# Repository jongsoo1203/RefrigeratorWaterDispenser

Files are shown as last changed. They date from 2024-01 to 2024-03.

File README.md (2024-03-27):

# 🛜 Smart Refrigerator Water Dispenser

Schematics, code, [Web-app](https://github.com/loty2019/water-dispenser-web) and [3D files](https://github.com/loty2019/RefrigeratorWaterDispenser/tree/RelayWaterDispenser/STL%20files) all available.

## ℹ️ Overview
This project aims to automate the refrigerator water dispenser. Originally located inside the fridge, it has been moved outside using a custom 3D-designed fountain. We first prototyped it on Arduino and then transitioned to the ESP32 platform with internet capabilities. The entire system now operates on a real-time database hosted on Firebase.

### Purpose (Why should this exist?)

The fridge has an internal water dispensing system that is manual. You have to hold the water bottle up, then at the same time press a hard button. In this process, the refrigerator loses coldness, and you get cold. Our system, however, utilizes an external custom-designed fountain that provides cold water after just 2 seconds of water flowing with no need to hold or press anything.

## 🗂️ Features

### 1. Remote Control

Our system reads signals from a remote controller, a simple numeric keypad used to navigate menus, set parameters, and choose which water bottle to fill and how.

### 2. Display

The 1602 display with I2C protocol provides real-time information.

### 3. Motion Activation

We've integrated a motion sensor that wakes the device from deep sleep only when someone approaches for water, enhancing energy efficiency.

### 4. Web App

We chose to use Next.js, React and Tailwind CSS to develop a simple yet useful UI to keep track of the water consumption of each user.

### 5. Custom Feature

Hosting guests or following a recipe that demands an exact amount of water? Input the desired ounces, enable unlimited fill, and so on... a handy extra feature for any occasion.

### 6. Relay

To communicate with the fridge on when to open the flow, we decided to use a relay since it allows handling 120V currents with just a 3.3V board.

### 7. Internet

Everything from water consumption to settings will be stored on a Firebase real-time database.

## Settings, Error Handling, and Details

We calculated the dispenser's flow rate and programmed the ESP to adjust the dispensing time accordingly. The user can also adjust it, and everything will be stored on the Flash memory and the database.

### Error Documentation:
Error #01 = Failed to record individual water consumption.

Error #02 = Failed to push consumption to the database.

Error #03 = Failed to generate date or hour due to connection issues.

Others coming soon...

### How to Build (soldering might be required)

- Follow the schematics and picture attached below (these are for the prototype) if you are not using the I2C protocol to cominicate with the display then use a NPN transistor to turn off the screen.
  I actually used a 3 pin relay so the image below is not accurate

[Water Dispenser.pdf](https://github.com/loty2019/RefrigeratorWaterDispenser/files/13521786/Water.Dispenser.pdf)

- 3D printable files are in STL_files folder
3D design
fusion fauntain v2

- Set up a database and a web app

Screenshot 2024-03-16 at 11 35 05 AM

- Final Product


https://github.com/loty2019/RefrigeratorWaterDispenser/assets/125715080/05de6919-4a6a-43a9-aefa-cd7f2b6fba2c

Collaboration: Lorenzo, Jongsoo, Minh

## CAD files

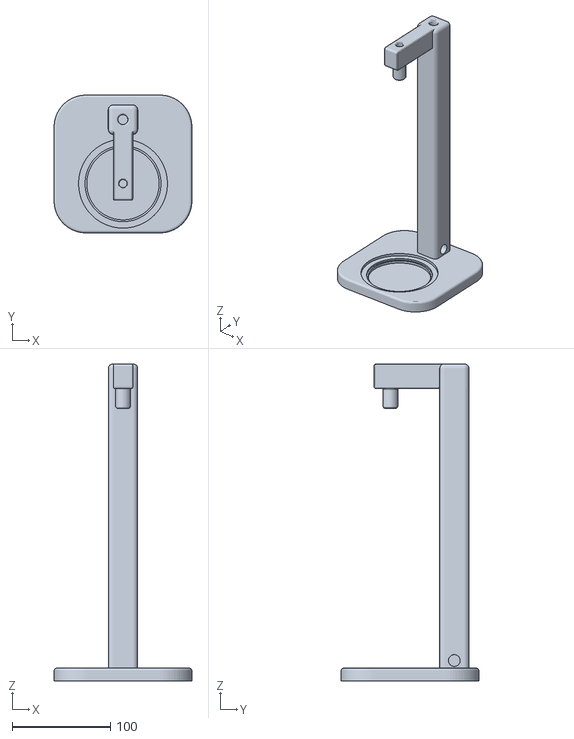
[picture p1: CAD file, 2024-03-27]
STL files/fauntain v2.stl
140.0 x 140.0 x 321.9

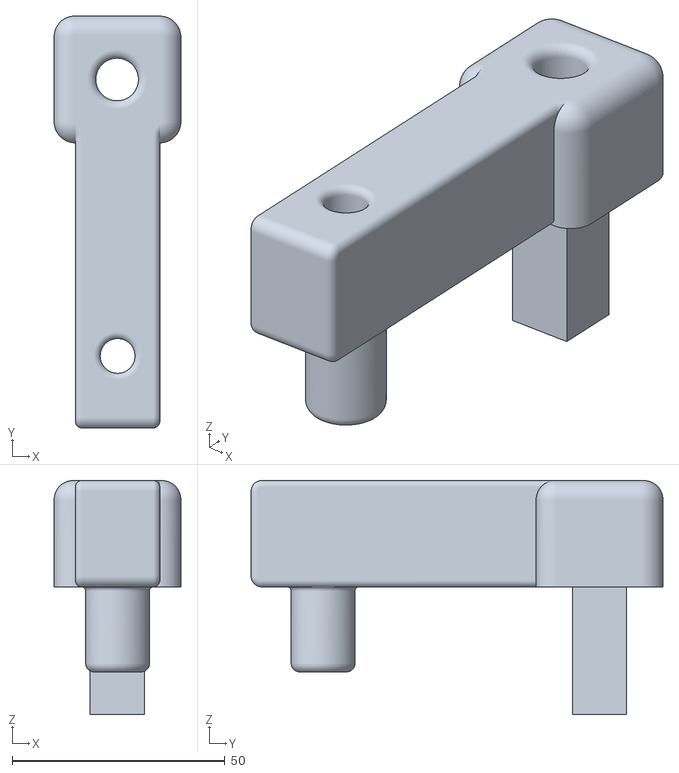
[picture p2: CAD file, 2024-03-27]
STL files/head v2.stl
29.8 x 96.8 x 55.0

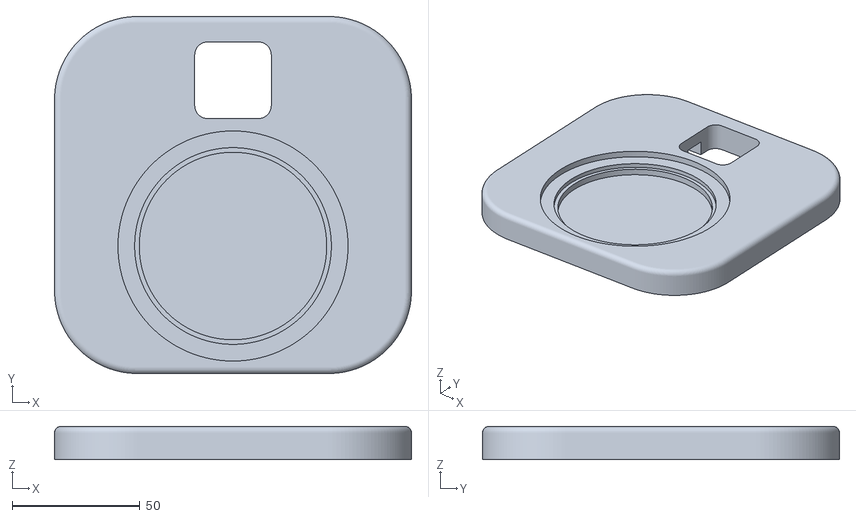
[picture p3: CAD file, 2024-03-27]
STL files/base v2.stl
140.0 x 140.0 x 13.0

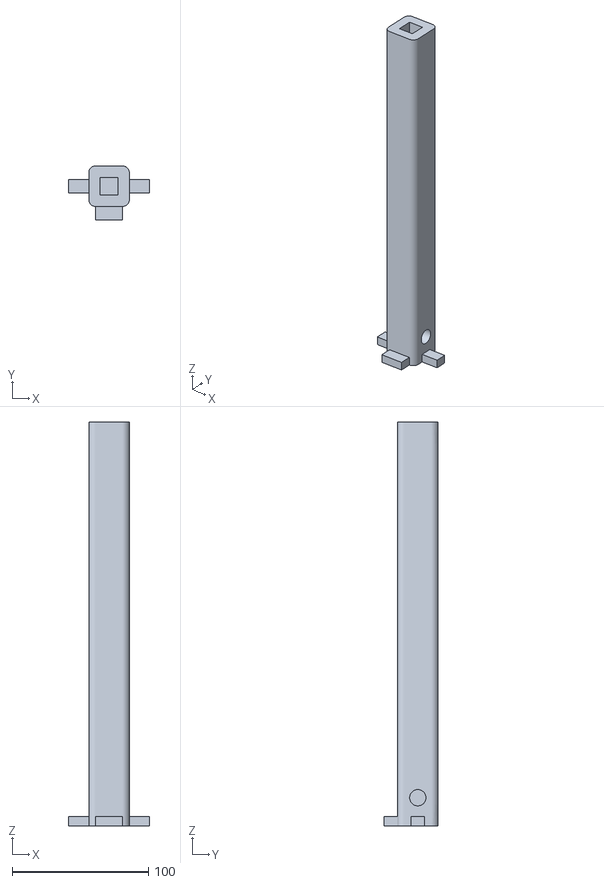
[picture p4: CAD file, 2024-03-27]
STL files/Arm v2.stl
59.9 x 39.8 x 297.0

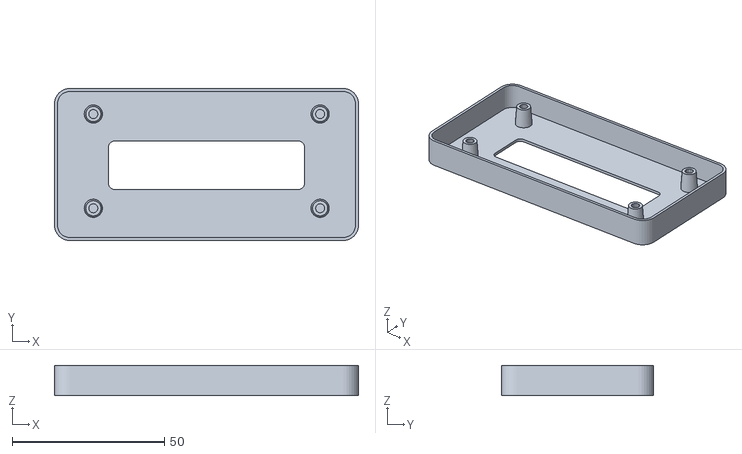
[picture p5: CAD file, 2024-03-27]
STL files/parametric_alphanumeric_display_faceplate.stl
100.0 x 50.0 x 10.0

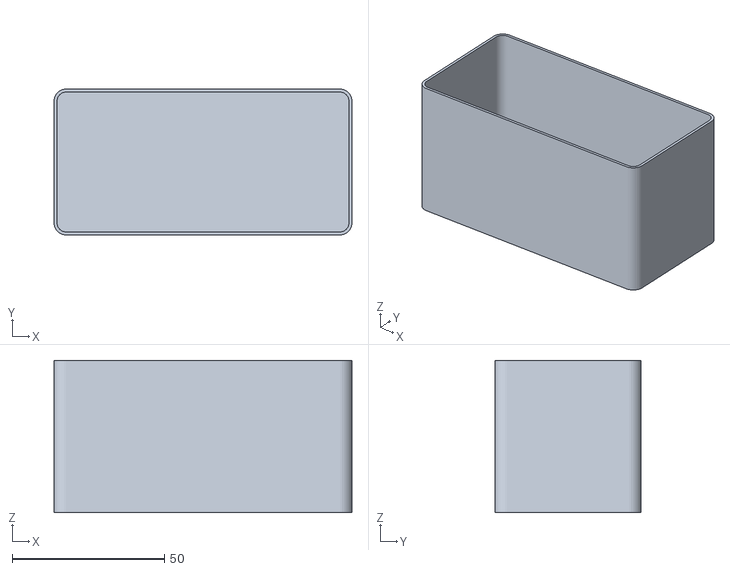
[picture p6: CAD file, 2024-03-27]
STL files/rounded_case.stl
98.0 x 48.0 x 50.0

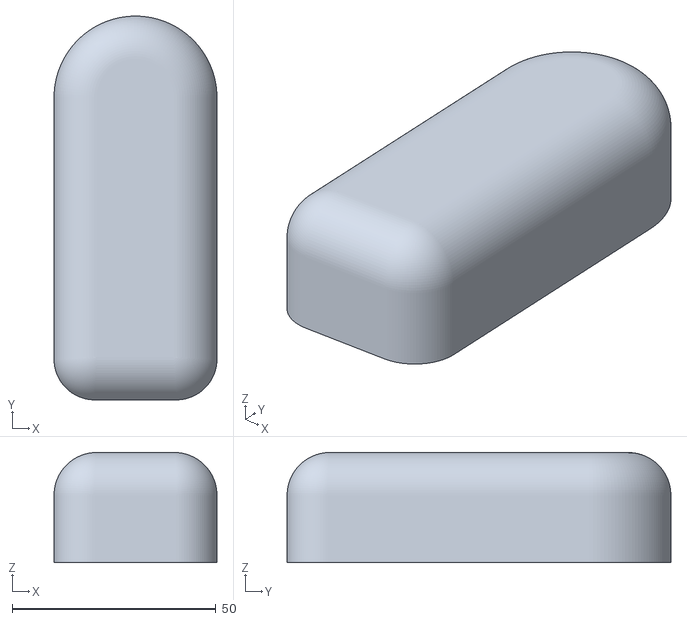
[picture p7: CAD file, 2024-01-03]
STL files/top.stl
40.0 x 94.2 x 27.0

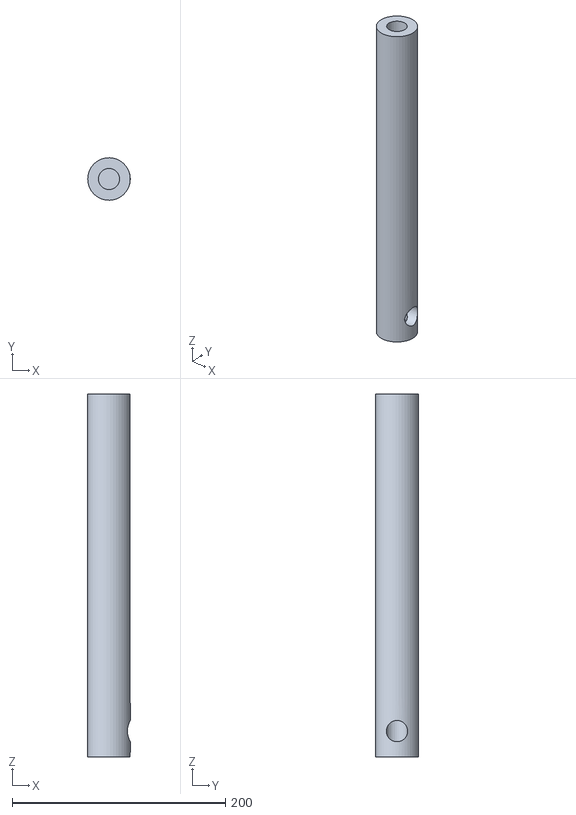
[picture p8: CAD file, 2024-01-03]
STL files/stand.stl
39.9 x 39.9 x 340.1

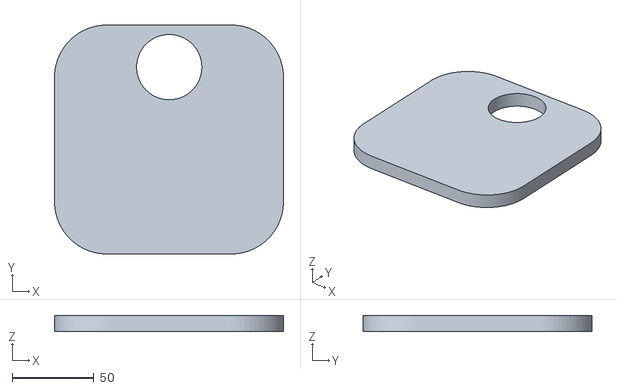
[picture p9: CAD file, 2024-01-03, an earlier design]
STL files/Base.stl
140.0 x 140.0 x 10.0

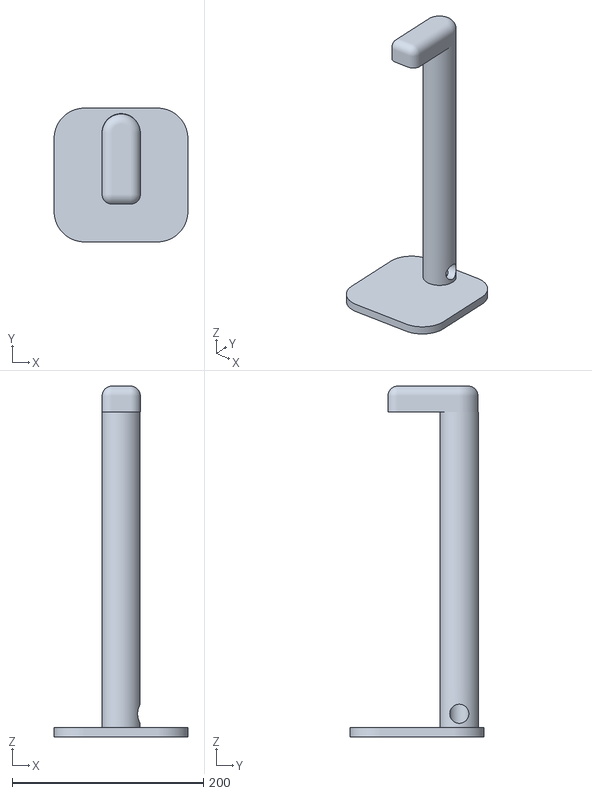
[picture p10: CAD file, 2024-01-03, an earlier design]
STL files/fauntain v1.stl
140.0 x 140.0 x 367.1

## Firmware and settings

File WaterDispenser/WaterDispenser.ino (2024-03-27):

// Error Doc:
// Error#01 = failed to record individual water 
// Error#02 = failed to push total consumption on database
// Error#03 = failed to generate date or hour due to connection issue


// Note to self: compile with ESP32-WROOM-DA with Baud Rate = 115200

// ******* MODIFY FOR NEW WATER BOTTLE (USE OZ) *******
const float LoreWHydroFlask = 24;
const float LaciHydroFlask = 32;
const float glassOfWater = 12;
// *****************************************

const char* textArray1[] = {
  "Press 1 for",
  "Press 2 for",
  "Press 4 for",
  "Press 0 for",
  "Press # for",
  "Press * for"
};
const char* textArray2[] = {
  "Lorenzo's Bottle",
  "Laci's Bottle",
  "Glass of Water",
  "Unlimited Fill",
  "Custom Oz Fill",
  "Flow Menu"
};

// ************************************
#include <ESP32Firebase.h>
#include <IRremote.h>
#include <time.h>
#include <LCD_I2C.h>
#include <Arduino.h>
#include <Wire.h>
#include <EEPROM.h>
#include <math.h>
#include <esp_sleep.h>

#define _SSID "IoT"          // Your WiFi SSID
#define _PASSWORD "BigKhauna69"      // Your WiFi Password
#define REFERENCE_URL "waterdispenserarduino-default-rtdb.firebaseio.com"  // Your Firebase project reference url
#define uS_TO_S_FACTOR 1000000ULL

struct tm timeinfo;
IRrecv IR(27);
Firebase firebase(REFERENCE_URL);
LCD_I2C lcd(0x27, 16, 2);

const int buzzer = 13;
const int relay = 26;
unsigned long lcdUpdateTime = 0;
int currentTextIndex1,currentTextIndex2  = 0;
const int motionPin = 25;
unsigned long lastMotionTime = 0;
const unsigned long motionDelay = 150000; // 2.5 minutes to screen off 

// wake up timer selection
int wakeHour = 0;
int wakeMinute = 0;
int wakeSeconds = 0;

float foreverTotal = 0;
bool alreadyDoneReset = false;
uint64_t microSecondsUntilNextMidnight = 0;

void setup() {
  Serial.begin(115200);
  WiFi.mode(WIFI_STA);
  WiFi.disconnect();
  pinMode(buzzer, OUTPUT);
  pinMode(relay, OUTPUT);
  pinMode(motionPin, INPUT);
  // To get the input from the remote control
  IR.enableIRIn();
  lcd.begin();
  lcd.backlight();
  Wire.begin();
  delay(100);

  // Connect to WiFi
  //Serial.print("Connecting to: ");
  lcd.println("Connecting WIFI ");
  lcd.setCursor(0,1);

  Serial.println(_SSID);
  WiFi.begin(_SSID, _PASSWORD);

  int overflowCount = 0;
  while (WiFi.status() != WL_CONNECTED) {
    delay(500);
    //Serial.print("-");
    lcd.print("-");
    overflowCount+= 1;
    if (overflowCount >= 16) {
      ESP.restart();
    }
  }

  // Initialize time with NTP
  configTime(-5 * 3600, 0, "pool.ntp.org", "time.nist.gov");
  
  //Serial.println("Waiting for time");
  while (!getLocalTime(&timeinfo)) {
    delay(300);
  }
}

void loop() {
  updateLCD();
  checkIRInput();
  motionDetection();

  // time_t now = mktime(&timeinfo);
  // struct tm midnightTime = timeinfo;
  // midnightTime.tm_hour = wakeHour;
  // midnightTime.tm_min = wakeMinute;
  // midnightTime.tm_sec = wakeSeconds;
  // time_t midnight = mktime(&midnightTime);
  // long timeToMidnight = difftime(midnight, now);

  // //Serial.println(String(timeToMidnight));

  // if (abs(timeToMidnight) <= 60) {
  //   lcd.clear();
  //   lcd.print("Resetting...");
  //   lcd.setCursor(0, 1);
  //   lcd.print("Please Wait");
  //   // The current time is within the range 00:00 to 00:01
  //   // Execute Reset operation for website purpose 
  //   if (getLocalTime(&timeinfo)) {
  //     if (firebase.setInt("/records/" + formatDate(&timeinfo) + "/lorenzo/" + formatTime(&timeinfo), 0) && firebase.setInt("/records/" + formatDate(&timeinfo) + "/laci/" + formatTime(&timeinfo), 0)) {
  //       foreverTotal = firebase.getFloat("/records/forever_consumption");
  //       foreverTotal += LoreWHydroFlask;
  //       if (firebase.setFloat("/records/forever_consumption", foreverTotal)) {
  //         //Serial.println("Firebase Push Successful");
  //         lcd.clear();
  //         lcd.setCursor(0, 0);
  //         lcd.print("Reset Success");
  //         delay(2000);
  //       } else {
  //         lcd.print("Pushed Failed");
  //         lcd.setCursor(0, 1);
  //         lcd.print("Error#02");
  //         delay(2000);
  //       }
  //     } else {
  //       lcd.print("Pushed Failed");
  //       lcd.setCursor(0, 1);
  //       lcd.print("Error#01");
  //       delay(2000);
  //     }
  //   }
  //   lcd.clear();
  //   lcd.print("Resetting...");
  //   lcd.setCursor(0, 1);
  //   lcd.print("Please Wait");
  //   delay(60000);
  //   ESP.restart();
  // }
  if (WiFi.status() != WL_CONNECTED) {
    ESP.restart();
  }
}

void motionDetection() {
  int motionState = digitalRead(motionPin); // Read sensor state
  //Serial.println(motionState);
  if (motionState == HIGH /*&& !lcdResetFlag*/) {
    //Serial.println("Motion detected!");
    //digitalWrite(LCDLight, LOW); // Activate display when motion is detected
    lastMotionTime = millis();// Record the time of the last motion detection
    lcd.backlight();
    lcd.display();
    //lcdResetFlag = true;
  } else {
    //Serial.println("No motion detected.");
    // Check if the elapsed time since the last motion is greater than the delay
    if (millis() - lastMotionTime > motionDelay) {
      //Serial.println("Going to sleep..."); 
      //lcdResetFlag = false;
      lcd.noBacklight();
      lcd.noDisplay(); // De-activate display when motion is not detected
      //Serial.flush(); 
      //esp_deep_sleep_start();
      //esp_light_sleep_start();
    }
  }
}

void checkIRInput() {
  // Update the current date and time
  float ozNew;
  bool recieved = false;
  if (IR.decode()) {
    // Convert the signal value to a number
    Serial.println(IR.decodedIRData.decodedRawData, HEX);
    // Remote input cases
    switch (IR.decodedIRData.decodedRawData) {
      case 0xE916FF00: // 1 my water
        doubleBeepSound();
        if (getLocalTime(&timeinfo)) {
          lcd.clear();
          lcd.print("Loading...");
          flowing(getSeconds(LoreWHydroFlask), LoreWHydroFlask);
          lcd.print("Loading...");
          if (firebase.setInt("/records/" + formatDate(&timeinfo) + "/lorenzo/" + formatTime(&timeinfo), LoreWHydroFlask)){
            foreverTotal = firebase.getFloat("/records/forever_consumption");
            foreverTotal += LoreWHydroFlask;
            if (firebase.setFloat("/records/forever_consumption", foreverTotal)) {
              //Serial.println("Pushed Success");
              lcd.setCursor(0, 1);
              lcd.print("Pushed Success");
              delay(2000);
            } else {
              Serial.println("Pushed Failed Error#02");
              lcd.print("Pushed Failed");
              lcd.setCursor(0, 1);
              lcd.print("Error#02");
              delay(2000);
            }
          } else {
            Serial.println("Pushed Failed Error#01");
            lcd.print("Pushed Failed");
            lcd.setCursor(0, 1);
            lcd.print("Error#01");
            delay(2000);
          }
        }
        break;
      case 0xE619FF00: // 2 laci water
        doubleBeepSound();
        if (getLocalTime(&timeinfo)) {
          lcd.clear();
          lcd.print("Loading...");
          flowing(getSeconds(LaciHydroFlask), LaciHydroFlask);
          lcd.print("Loading...");
          if (firebase.setInt("/records/" + formatDate(&timeinfo) + "/laci/" + formatTime(&timeinfo), LaciHydroFlask)){
            foreverTotal = firebase.getFloat("/records/forever_consumption");
            foreverTotal += LaciHydroFlask;
            if (firebase.setFloat("/records/forever_consumption", foreverTotal)) {
              //Serial.println("Pushed Success");
              lcd.setCursor(0, 1);
              lcd.print("Pushed Success");
              delay(2000);
            } else {
              Serial.println("Pushed Failed Error#02");
              lcd.print("Pushed Failed");
              lcd.setCursor(0, 1);
              lcd.print("Error#02");
              delay(2000);
            }
          } else {
            Serial.println("Pushed Failed Error#01");
            lcd.print("Pushed Failed");
            lcd.setCursor(0, 1);
            lcd.print("Error#01");
            delay(2000);
          }
        }
        break;
      
      case 0xF30CFF00: // 4
          doubleBeepSound();
          lcd.clear();
          lcd.print("Loading...");
          flowing(getSeconds(glassOfWater), glassOfWater);
          break;
      case 0xAD52FF00: // 0
        singleBeepSound();
        digitalWrite(relay, !digitalRead(relay));
        break;
      case 0xB54AFF00: // # custom fill
        //Serial.println("# RECIEVED");
        // increase performance and user expirience but worst memory 
        ozNew = customFilling();
        if (ozNew != 0) {
          // assign water consumprio to the person
          lcd.clear();
          lcd.print("Record it ?");
          lcd.setCursor(0, 1);
          lcd.print("# to cancel");
          // loop wait for user input
          while (!recieved) {
            if (IR.decode()) {
              if (IR.decodedIRData.decodedRawData == 0xBF40FF00) { // if ok is pressed
                doubleBeepSound();
                lcd.clear();
                lcd.print("Press ur number");
                lcd.setCursor(0, 1);
                lcd.print("to record data..");
                while (!recieved) {
                  if (IR.decode()) {
                    switch (IR.decodedIRData.decodedRawData) {
                      case 0xE916FF00: // 1 my water
                        doubleBeepSound();
                        lcd.clear();
                        lcd.print("Loading...");
                        if (firebase.setInt("/records/" + formatDate(&timeinfo) + "/lorenzo/" + formatTime(&timeinfo), ozNew)){
                          foreverTotal = firebase.getFloat("/records/forever_consumption");
                          foreverTotal += ozNew;
                          firebase.setFloat("/records/forever_consumption", foreverTotal);

                          Serial.println("Pushed Success");
                          lcd.setCursor(0, 1);
                          lcd.print("Pushed Success");
                          delay(2000);
                        } else {
                          Serial.println("Pushed Failed Error#01");
                          lcd.print("Pushed Failed");
                          lcd.setCursor(0, 1);
                          lcd.print("Error#01");
                          delay(2000);
                        }
                        recieved = true;
                        break;
                      case 0xE619FF00: // 2 laci water
                        doubleBeepSound();
                        lcd.clear();
                        lcd.print("Loading...");
                        if (firebase.setInt("/records/" + formatDate(&timeinfo) + "/lorenzo/" + formatTime(&timeinfo), ozNew)){
                          foreverTotal = firebase.getFloat("/records/forever_consumption");
                          foreverTotal += ozNew;
                          firebase.setFloat("/records/forever_consumption", foreverTotal);

                          //Serial.println("Pushed Success");
                          lcd.setCursor(0, 1);
                          lcd.print("Pushed Success");
                          delay(2000);
                        } else {
                          //Serial.println("Pushed Failed Error#01");
                          lcd.print("Pushed Failed");
                          lcd.setCursor(0, 1);
                          lcd.print("Error#01");
                          delay(2000);
                        }
                        recieved = true;
                        break;
                    }
                    delay(500);
                    IR.resume();
                  }
                }
              }
              // if # we brake and exit the loop
              else if (IR.decodedIRData.decodedRawData == 0xB54AFF00) {
                doubleBeepSound();
                lcd.clear();
                recieved = true;
                break;
              }
              delay(200);
              IR.resume();
            }
          }
        }
        break;
      
      
      case 0xBD42FF00: // * menu 
        flowMenu();
        break;
    }
    delay(100);
    IR.resume();
  }
}

void flowMenu() {
  doubleBeepSound();
  lcd.clear();
  lcd.setCursor(0, 0);
  float SecForOunce = firebase.getFloat("/flow");
  float flow = SecForOunce; // redundancy for any change check before exiting
  lcd.print("Flow rate: " + String(SecForOunce));
  bool check = true;
  while (check) {
    if (IR.decode()) {
      // Remote input cases
      switch (IR.decodedIRData.decodedRawData) {
        case 0xB946FF00: // up button
          singleBeepSound();
          flow += 0.01;
          lcd.clear();
          lcd.print("Flow rate: " +  String(flow));
          break;
        case 0xEA15FF00: // down button
          singleBeepSound();
          flow -= 0.01;
          lcd.clear();
          lcd.print("Flow rate: " +  String(flow));
          break;
        case 0xBF40FF00: // OK when done
          doubleBeepSound();
          doubleBeepSound();
          if (SecForOunce != flow){
            if (firebase.setFloat("/flow", flow)) {
                lcd.clear();
                //Serial.println("Pushed Success");
                lcd.print("Pushed Success");
                delay(2000);
            } else {
              //Serial.println("Pushed Failed Error#02");
              lcd.clear();
              lcd.print("Pushed Failed");
              lcd.setCursor(0, 1);
              lcd.print("Error#02");
              delay(2000);
            }
            lcd.clear();
            //Serial.println("New flow rate set ");
            lcd.print("New flow rate");
            lcd.setCursor(0, 1);
            lcd.print("stored");
            delay(1000);
          }
          check = false;
          break;
      }
      delay(50);
      IR.resume();
    }
  }
}

void updateLCD() {
  if (millis() - lcdUpdateTime >= 3000) {
    lcd.clear();
    lcd.setCursor(0, 0);
    lcd.print(textArray1[currentTextIndex1]);

    currentTextIndex1 = (currentTextIndex1 + 1) % (sizeof(textArray1) / sizeof(textArray1[0]));  // Cycle through textArray
    lcd.setCursor(0, 1);
    lcd.print(textArray2[currentTextIndex2]);
    currentTextIndex2 = (currentTextIndex2 + 1) % (sizeof(textArray2) / sizeof(textArray2[0]));
    lcdUpdateTime = millis();
  }
}

void clearSecondLine() {
  lcd.setCursor(0, 1);
  lcd.print("                ");  // Print spaces to clear the second line
}

float customFilling() {
  doubleBeepSound();

  const char* unitMeasure[] = {
    "oz",
    "cups",
    "mL"
  };
  // if anything gets added only need to change output 'if'
  int unitMeasureIndex = 0;

  String resultStr = "";
  bool check = true;
  bool panic = false;
  lcd.clear();
  lcd.println("OK=Done   #=Canc");
  IR.resume();
  while (check) {
    if (IR.decode()) {
      // Remote input cases
      switch (IR.decodedIRData.decodedRawData) {
        case 0xE916FF00: // 1
          singleBeepSound();
          resultStr += "1";
          clearSecondLine();
          lcd.setCursor(0, 1);
          lcd.print(resultStr + unitMeasure[unitMeasureIndex]);
          break;
        case 0xE619FF00: // 2
          singleBeepSound();
          resultStr += "2";
          clearSecondLine();
          lcd.setCursor(0, 1);
          lcd.print(resultStr + unitMeasure[unitMeasureIndex]);
          break;
        case 0xF20DFF00: // 3
          singleBeepSound();
          resultStr += "3";
          clearSecondLine();
          lcd.setCursor(0, 1);
          lcd.print(resultStr + unitMeasure[unitMeasureIndex]);
          break;
        case 0xF30CFF00: // 4
          singleBeepSound();
          resultStr += "4";
          clearSecondLine();
          lcd.setCursor(0, 1);
          lcd.print(resultStr + unitMeasure[unitMeasureIndex]);
          break;
        case 0xE718FF00: // 5
          singleBeepSound();
          resultStr += "5";
          clearSecondLine();
          lcd.setCursor(0, 1);
          lcd.print(resultStr + unitMeasure[unitMeasureIndex]);
          break;
        case 0xA15EFF00: // 6
          singleBeepSound();
          resultStr += "6";
          clearSecondLine();
          lcd.setCursor(0, 1);
          lcd.print(resultStr + unitMeasure[unitMeasureIndex]);
          break;
        case 0xF708FF00: // 7
          singleBeepSound();
          resultStr += "7";
          clearSecondLine();
          lcd.setCursor(0, 1);
          lcd.print(resultStr + unitMeasure[unitMeasureIndex]);
          break;
        case 0xE31CFF00: // 8
          singleBeepSound();
          resultStr += "8";
          clearSecondLine();
          lcd.setCursor(0, 1);
          lcd.print(resultStr + unitMeasure[unitMeasureIndex]);
          break;
        case 0xA55AFF00: // 9
          singleBeepSound();
          resultStr += "9";
          clearSecondLine();
          lcd.setCursor(0, 1);
          lcd.print(resultStr + unitMeasure[unitMeasureIndex]);
          break;
        case 0xAD52FF00: // 0
          singleBeepSound();
          resultStr += "0";
          clearSecondLine();
          lcd.setCursor(0, 1);
          lcd.print(resultStr + unitMeasure[unitMeasureIndex]);
          break;
        case 0xBF40FF00: // OK when done
          singleBeepSound();
          lcd.clear();
          //Serial.println("OK recieved");
          lcd.print(resultStr + unitMeasure[unitMeasureIndex] + "Confirmed");
          delay(500);
          check = false;
          break;
        case 0xB54AFF00: // #
          panic = true;
          lcd.clear();
          lcd.print("CANCELLED");
          doubleBeepSound();
          delay(50);
          doubleBeepSound();
          check = false;
          break;
        case 0xBD42FF00: // *
          singleBeepSound();
          resultStr += ".";
          clearSecondLine();
          lcd.setCursor(0, 1);
          lcd.print(resultStr + "oz");
          break;
        case 0xB946FF00: // up button
          break;
        case 0xEA15FF00: // down button
          break;
        case 0xBB44FF00: // left button
          singleBeepSound();
          unitMeasureIndex -= 1;
          if (unitMeasureIndex < 0) {
            unitMeasureIndex = sizeof(unitMeasure) / sizeof(unitMeasure[0]) - 1;
          }
          clearSecondLine();
          lcd.setCursor(0, 1);
          lcd.print(resultStr + unitMeasure[unitMeasureIndex]);
          break;
        case 0xBC43FF00: // right button
          singleBeepSound();
          unitMeasureIndex += 1;
          if (unitMeasureIndex >= sizeof(unitMeasure) / sizeof(unitMeasure[0])) {
            unitMeasureIndex = 0;
          }
          clearSecondLine();
          lcd.setCursor(0, 1);
          lcd.print(resultStr + unitMeasure[unitMeasureIndex]);
          break;
      }
      delay(200);
      IR.resume();
    }
  }
  if (panic == false) {
    //Serial.println(resultStr);
    float resultFloat = resultStr.toFloat(); // transloate to float

    if (strcmp(unitMeasure[unitMeasureIndex], "oz") == 0){ // check unit measures
      flowing(getSeconds(resultFloat), resultFloat);
    } else if (strcmp(unitMeasure[unitMeasureIndex], "cups") == 0) {
      resultFloat = resultFloat*8; // to get oz
      flowing(getSeconds(resultFloat), resultFloat);
    } else if (strcmp(unitMeasure[unitMeasureIndex], "mL") == 0) {
      resultFloat = resultFloat * 0.0338;
      flowing(getSeconds(resultFloat), resultFloat);
    }
    return(resultFloat);
  }
  return 0;
}

String formatTime(struct tm* timeinfo) {
  char formattedTime[10];
  strftime(formattedTime, sizeof(formattedTime), "%H:%M:%S", timeinfo);
  return String(formattedTime);
}

String formatDate(struct tm* timeinfo) {
  char formattedDate[15];
  strftime(formattedDate, sizeof(formattedDate), "%Y-%m-%d", timeinfo);
  return String(formattedDate);
}
// beep beep sound
void doubleBeepSound() {
  digitalWrite(buzzer, HIGH);
  delay(100);
  digitalWrite(buzzer, LOW);
  delay(50);
  digitalWrite(buzzer, HIGH);
  delay(100);
  digitalWrite(buzzer, LOW);
}

void flowing(int bottle, float oz){
  // sequent to pur the water 
  // starting sound
  doubleBeepSound();
  // relay activation
  digitalWrite(relay, HIGH); // Connects the external wires
  displayLoadingBar(bottle, oz); // wait x time
  digitalWrite(relay, LOW); // Disconnects the external wires
  // end sound
  doubleBeepSound();
  lcd.print("!!!!! DONE !!!!!");
  delay(2000);
  lcd.clear();
  lcd.setCursor(0, 0);
}

float getSeconds(float oz) {
  return oz * (firebase.getFloat("/flow")); // it takes 2 second to get 1 ounce
}

// loading bar that will last x seconds
void displayLoadingBar(float seconds, float oz) {
  lcd.clear();
  int barLength = 16; // Number of characters in the loading bar
  float delayTime = seconds * 1000.0 / barLength; // Calculate delay time for each step
  lcd.print("Filling " + String(oz) + "oz");
  lcd.setCursor(0, 1); // Move cursor to the second line
  for (int i = 0; i < barLength; ++i) {
    //lcd.print("#");
    lcd.write(0xFF); // full block characheter 
    delay((int)delayTime); // Convert delayTime to an integer before using it in delay()
  }
  lcd.clear();
}

// single beep sound
void singleBeepSound(){
  digitalWrite(buzzer, HIGH);
  delay(100);
  digitalWrite(buzzer, LOW);
}

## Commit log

2023-11-26 New code for relay
    added the new code
2023-11-26 original file
    Original file with editing Arduino setup.
2023-12-01 stl files
    stl files for 3d printing
    [Base.stl, stand.stl, top.stl]
2023-12-01 stl update
    [fauntain v1.stl]
2023-12-15 New features
    All bugs fixed, better menu, more responsive, more power efficient, better organized.
    [WaterDispenser.ino]
2024-01-18 feature: server & midnight reset
    [WaterDispenser.ino]
2024-03-09 Fix: loop freezing fixed
    [WaterDispenser.ino]
2024-03-11 new stl files
    [parametric_alphanumeric_display_faceplate.stl, rounded_case.stl]
2024-03-27 Improved code stability
    Also added a new stl model
    [Arm v2.stl, base v2.stl, fauntain v2.stl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]
